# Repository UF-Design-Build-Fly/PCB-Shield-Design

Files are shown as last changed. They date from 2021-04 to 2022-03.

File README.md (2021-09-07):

# PCB-Shield-Design Description
Custom "Shield" Design to be mounted on MicroMod ATP Carrier board seen in Avionics Repo. Here are its [dimensions](https://cdn.sparkfun.com/assets/4/8/6/f/7/MicroMod_ATP_Carrier_Board_Dimensions.png).

## Features v2
- Sensors on board: IMU, pressure, temperature, voltage, current, airspeed. 
- 3 pin connectors for servos. 
- PWM signals from receiver are wired to the board and routed to the servos.
- Female headers will connect the shield to the carrier board (stacking boards).
- PWM signals will be wired to I/O pins to be read and logged.
- Micro SD will be used for data logging.
- Power for avionics and servos will be separate.
- Step down buck converter will be used to regulate a 5V supply voltage on the board (5V will also be fed to VIN for carrier board to be stepped down to 3.3V).
- Mounting holes on corners of the board (100 mil diameter).
- 2 LED light indicators to communicate state of device.

TOP 3D             |  TOP PCB
:-------------------------:|:-------------------------:
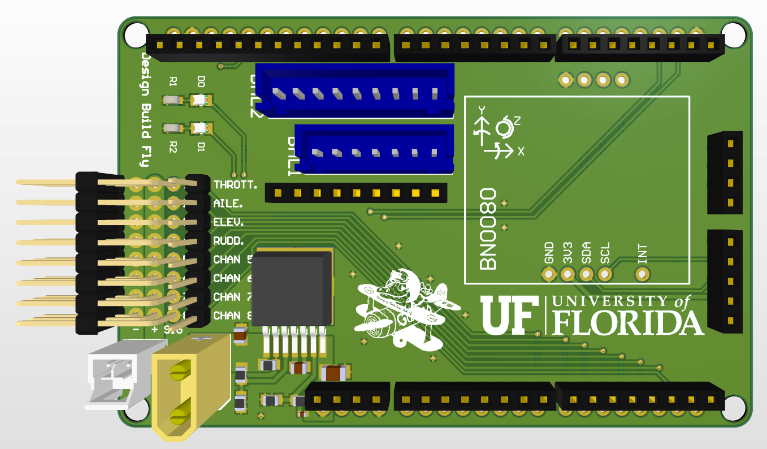
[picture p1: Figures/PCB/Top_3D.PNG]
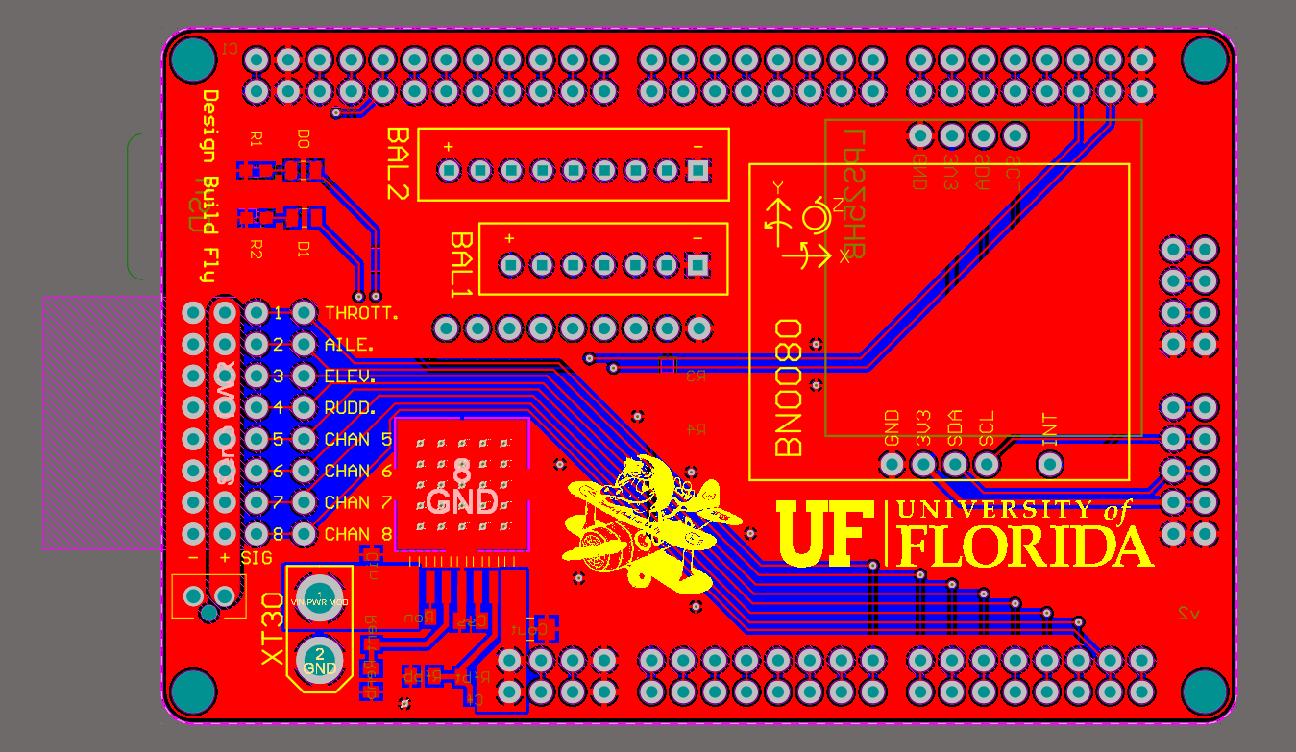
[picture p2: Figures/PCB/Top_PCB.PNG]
  |  

BOTTOM 3D             |  BOTTOM PCB
:-------------------------:|:-------------------------:
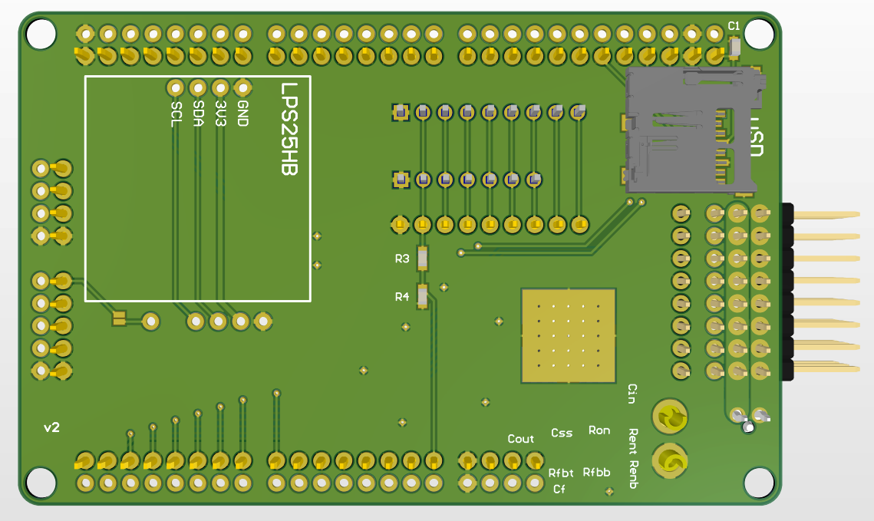
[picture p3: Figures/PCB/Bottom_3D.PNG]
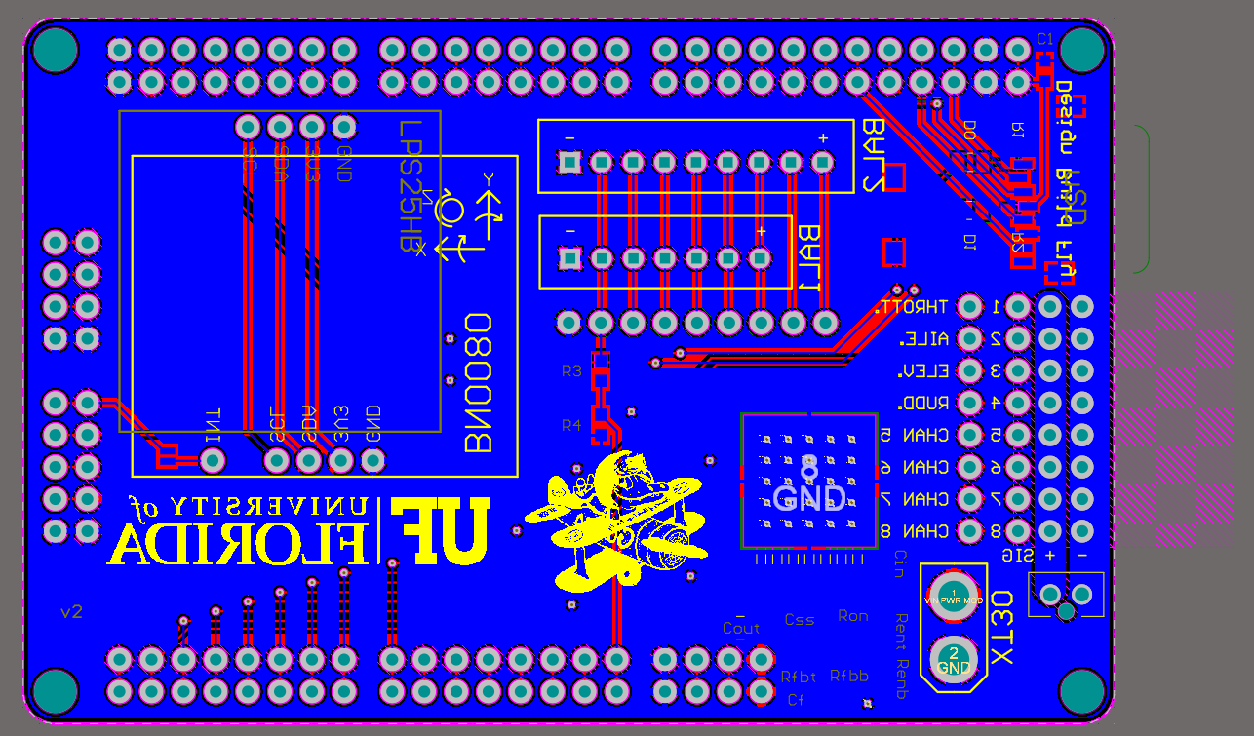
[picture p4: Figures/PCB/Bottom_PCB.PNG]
  |  

## v3 Revisions
- Remove unnecessary parts on PCB: JST connectors for battery balance leads, alarm connector, voltage divider for monitoring 1st cell on battery, any useless female connectors that can free up space (e.g. we are not using I2S connectors or any UART but we are using I2C, etc.).
- Remove solder mask on servo PWR and GND. Change trace width to somewhere between 80 and 90 mil. Decide whether custom copper bus bar or a layer of solder will be used to increase the amount of current the traces can carry. Solder can be around 10 times less conductive resulting in greater power loss, but it is the simpler solution (silver solder is only around 5 to 2.5 times less conductive). Copper bus bar is the more complex solution and involves machining or plasma cutting bus bars from sheets of copper and then connecting them to the board with a thin layer of solder for an adequate connection. This solution provides better power delivery and will result in less heat being generated. Or we can just add a wire on top for the pins ```\ ___ :/ ___ /````
- Add connectors for airspeed sensor and voltage/current sensor
- Look at signal connections between receiver and board. Determine what type of molex connector should be used for a secure connection. 
- Decide on dedicated pin usage for PCB. 
- Should the width of the board be increased?
- Correct screw size for 0.1 inch.
- Servo PWR connector should be XT30
- Determine whether or not XT30 connectors should be horizontal and not vertical.
- Change Rfbb resistor (must be between 1k and 10k) on buck converter to a potentiometer. Probably buy a 2k potentiometer with a screw terminal. This allows us to tune the output voltage to 5V.
- Add power LED at Vout of LMZ12002
- Add piezo for sounds?

## Additional Ideas?
- Make another small board to send signals from angle of attack sensor

## Dedicated Pin Usage (e.g. General I/O, Analog and digital pins, SPI pins, I2C pins)
TBD

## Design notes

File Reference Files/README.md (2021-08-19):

## Viewing PCBs
If you do not have Altium Designer go to Altium Viewer to view the files under "Import Files": https://www.altium.com/viewer/#features

### Things to remember
- 1 mil = 1 thousandth of an inch
- Standard pitch is 0.1 inches or 2.54 mm
- SparkFun's hole shape is round, top: 74mil, hole size: 40mil

When needed, calculate trace width using this [webiste](https://www.4pcb.com/trace-width-calculator.html)'

## Connector Info
- Lipo Balance Leads: [JST-XH](https://www.digikey.com/catalog/en/partgroup/xh-series/2841)
  - [6s](https://www.digikey.com/en/products/detail/jst-sales-america-inc/B7B-XH-A-LF-SN/1651050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)
  - [8s](https://www.digikey.com/en/products/detail/jst-sales-america-inc/B9B-XH-A(LF)(SN)/1651042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)
  - [CAD files](https://www.jst-mfg.com/product/detail_e.php?series=277) for 6s and 8s connector
- Servo PWR connector (Header): [1053091202](https://www.digikey.com/en/products/detail/molex/1053091202/6131607)
- Servo PWR connector (Recepticle): [1053071202](https://www.molex.com/molex/products/part-detail/crimp_housings/1053071202)
- Servo PWR connector (Crimp Terminal): [1053002200](https://www.molex.com/molex/products/part-detail/crimp_terminals/1053002200)
- Other Power Connectors: [MOLEX](https://www.molex.com/molex/products/group/wire_to_board_connectors)

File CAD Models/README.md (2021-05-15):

## Links to external CAD files
Tripe row male header pins (pitch 2.54mm): https://grabcad.com/library/triple-row-male-pin-headers-1

XH Connector : https://www.jst-mfg.com/product/detail_e.php?series=277

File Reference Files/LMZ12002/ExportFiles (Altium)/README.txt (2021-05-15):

## WEBENCH Design 4
Created at Sat May 15 13:25:19 PDT 2021
**********************************************************
***************** Schematic Instructions  ****************
**********************************************************

To import your new Schematic into Altium:

1. Unzip the downloaded folder files to a local directory and 
   Start the Altium program.
2. From the menu select "File"->"Open".
3. Select the file named in the path above ending with ".schdoc"
   and "Open" the file.
4. Your Schematic should be viewable within Altium now.

For additional information, please visit this site:
http://www.accelerated-designs.com/help/Altium_BrdSch_import.html

**********************************************************
*******************  PCB Instructions  *******************
**********************************************************

To import your new BOARD into Altium:

1. Unzip the downloaded folder files to a local directory
	and Start the Altium program.
2. From the menu select "File"->"Open".
3. Select the file named in the path above ending with ".pcbdoc"
   and "Open" the file.
4. Planes will need to be repoured to update the Copper Pour Polygons
	a. Once your board is loaded, select the Tools menu from the
	   top Menu Bar
	b. Scroll to the Polygon Pours item on the Tools Menu.
	c. The Polygon Pours item should expand to show more options
	d. Select Repour All Polygons, this will repour all of the
	   polygons.
5. Your board should be viewable within Altium now.

For additional information, please visit this site:
http://www.accelerated-designs.com/help/Altium_BrdSch_import.html

**********************************************************
*******************  LIB Instructions  *******************
**********************************************************

To import your new LIBRARY PARTS into Altium follow these steps:

1. After running the Ultra Librarian export for the first time,
   you will need to copy the following files into an area where
   they can be accessed for all future translations.  They are script
   files that Altium will need to be able to find.
	a. UL_Form.dfm
	b. UL_Form.pas
	c. UL_Import.pas
	d. UL_Import.prjScr
2. The above script file will need to be run from within Altium.
   This can be done by going to File, Open and selecting the
   UL_Import.PrjScr file stored above.
3. Select the "DXP" dropdown menu in the top-left corner runfrom
   the drop down menu and select "Run Script". Select "UL_Form.pas"
   and click "OK"
4. When the script is run, it will ask you for the file name of the
   Ultra Librarian file to run. Click "File...", select the latest file
   produced with a date code (for instance 2010-02-17_23-12-34.txt), and
   click "Start Import".
5. The script will open a new Integraged Library project and import
   the Ultra Librarian data into it.  When complete a message box
   will pop up saying that import is done.

For additional information, please visit this site:
http://www.accelerated-designs.com/help/Altium_import.html

For a video tutorial, please visit:
http://youtu.be/pih50yx9HYU

**********************************************************
****************  SIMULATION Instructions  ***************
**********************************************************
This XML can be imported in Altium Designer 14 and higher using
WEBENCH Altium Connector Extension and simulated using WEBENCH
Simulation Engine.

The WEBENCH Altium Connector provides an interface to the
Texas Instruments WEBENCH Designer Tools as well as to open
WEBENCH exported Designs directly from inside Altium Designer.
It also includes the advanced WEBENCH Simulation Engine which
can be used for offline circuit simulations.

You will need to activate WEBENCH Altium Connector to be able
to use the WEBENCH Simulation Engine.

Installation guide:
http://www.ti.com/lit/SNVU481
You can download the WEBENCH extension from Altium Designer Extensions.

Connector Details:
http://www.ti.com/lsds/ti/analog/webench/altiumconnector.page

More about WEBENCH simulation export to Altium:
http://www.ti.com/lsds/ti/analog/webench/simexportaltium.page

User Manual:
http://www.ti.com/lit/szzu007

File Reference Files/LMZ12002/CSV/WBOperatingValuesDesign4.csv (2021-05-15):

Name | Value | Category | Description
Vout | 5 V | System Information | Operational Output Voltage
IC Tolerance | 20 mV | IC | IC Feedback Tolerance
Cin IRMS | 489.25 mA | Capacitor | Input capacitor RMS ripple current
Cin Pd | 957.44 µW | Capacitor | Input capacitor power dissipation
Cout IRMS | 119.17 mA | Capacitor | Output capacitor RMS ripple current
Cout Pd | 40.3 µW | Capacitor | Output capacitor power dissipation
Duty Cycle | 60.31% | System Information | Duty cycle
Efficiency | 91.8% | System Information | Steady state efficiency
Frequency | 488.71 kHz | System Information | Switching frequency
IC Tj | 43.6 °C | IC | IC junction temperature
ICThetaJA | 19.3 °C/W | IC | IC junction-to-ambient thermal resistance
IC Pd | 445.62 mW | IC | IC power dissipation
Pout | 5 W | System Information | Total output power
Iin Avg | 633.33 mA | IC | Average input current
IC Ipk | 1.21 A | IC | Peak switch current in IC
Mode | CCM | System Information | Conduction Mode
Vout p-p | 1.17 mV | System Information | Peak-to-peak output ripple voltage
M Vds Act | 130 mV | Mosfet | Voltage drop across the MosFET
M Irms | 852.42 mA | Mosfet | MOSFET RMS current
Total Pd | 446.62 mW | Power | Total Power Dissipation
FootPrint | 260 mm² | System Information | Total Foot Print Area of BOM components
Vin | 8.6 V | System Information | Vin operating point
Iout | 1 A | System Information | Iout operating point
Cin Pd | 957.44 µW | Power | Input capacitor power dissipation
Cout Pd | 40.3 µW | Power | Output capacitor power dissipation
IC Pd | 445.62 mW | Power | IC power dissipation
Vout Actual | 5 V | System Information | Vout Actual calculated based on selected voltage divider resistors
Vout Tolerance | 4.24% | System Information | Vout Tolerance based on IC Tolerance (no load) and voltage divider resistors if applicable
Total BOM | $4.66 | System Information | Total BOM Cost
BOM Count | 10 | System Information | Total Design BOM count

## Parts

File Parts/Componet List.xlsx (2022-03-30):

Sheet: PCB_Shield_v2
Componet Name | Manufacture No. | Description | Quantity | Unit Price | Link (if applicable) | Find Resistors: https://www.digikey.com/en/products/filter/chip-resistor-surface-mount/52
ERJ-3EKF1051V | ERJ-3EKF1051V | RES SMD 1.05K OHM 1% 1/10W 0603 | 1 | $0.10 | https://www.digikey.com/en/products/detail/panasonic-electronic-components/ERJ-3EKF1051V/196035 | Find Capacitors: https://www.digikey.com/en/products/filter/ceramic-capacitors/60
ERJ-3EKF3000V | ERJ-3EKF3000V | RES SMD 300 OHM 1% 1/10W 0603 | 1 | $0.10 | https://www.digikey.com/en/products/detail/panasonic-electronic-components/ERJ-3EKF3000V/1746363
RMCF0603JT10K0 | RMCF0603JT10K0 | RES 10K OHM 5% 1/10W 0603 | 2 | $0.10 | https://www.digikey.com/en/products/detail/stackpole-electronics-inc/RMCF0603JT10K0/1758104
LM338T/NOPB | LM338T/NOPB | IC REG LINEAR POS ADJ 5A TO220-3 | 1 | $2.23 | https://www.digikey.com/en/products/detail/texas-instruments/LM338T-NOPB/212669
CL10B104KB8NNNC | CL10B104KB8NNNC | CAP CER 0.1UF 50V X7R 0603 | 2 | $0.10 | https://www.digikey.com/en/products/detail/samsung-electro-mechanics/CL10B104KB8NNNC/3886658
CGB3B1X7R1A105K055AC | CGB3B1X7R1A105K055AC | CAP CER 1UF 10V X7R 0603 | 1 | $0.20 | https://www.digikey.com/en/products/detail/tdk-corporation/CGB3B1X7R1A105K055AC/3950464
MicroSD Socket | PRODUCT ID: 1660 | Add tons of storage to your next project with this micro SD card socket. We use this part in all our designs and it works great with any microSD ('transflash') of any storage size. It's a surface-mount part and the pins are underneath so it needs a fine tip and paste or thin solder to get in there and solder, not for beginners! It is a push-push type: push the card in to insert, push again to spring it out. | 1 | $1.95 | https://www.adafruit.com/product/1660
XT30 Connector (Male) | N/A | N/A | 1 | $0.39 | https://www.racedayquads.com/products/xt30-connector-male-or-female?_pos=11&_sid=ba0a2201c&_ss=r
S7B-XH-A(LF)(SN) | S7B-XH-A(LF)(SN) | CONN HEADER R/A 7POS 2.5MM | 1 | $0.61 | https://www.digikey.com.au/product-detail/en/jst-sales-america-inc/S7B-XH-A-LF-SN/455-2240-ND/1651038
B2B-XH-A(LF)(SN) | B2B-XH-A(LF)(SN) | CONN HEADER VERT 2POS 2.5MM | 1 | $0.15 | https://www.digikey.com/en/products/detail/jst-sales-america-inc/B2B-XH-A-LF-SN/1651045
LEDs w/ current limiting resistor | https://www.digikey.com/en/products/filter/led-indication-discrete/105
150080YS75000 | 150080YS75000 | LED YELLOW CLEAR 0805 SMD | 1 | $0.18 | https://www.digikey.com/en/products/detail/w%C3%BCrth-elektronik/150080YS75000/4489927
150080RS75000 | 150080RS75000 | LED RED CLEAR 0805 SMD | 1 | $0.18 | https://www.digikey.com/en/products/detail/w%C3%BCrth-elektronik/150080RS75000/4489918
150080VS75000 | 150080VS75000 | LED GREEN CLEAR 0805 SMD | 1 | $0.18 | https://www.digikey.com/en/products/detail/w%C3%BCrth-elektronik/150080VS75000/4489924
ERJ-3EKF66R5V | ERJ-3EKF66R5V | RES SMD 66.5 OHM 1% 1/10W 0603 | 3 | $0.10 | https://www.digikey.com/en/products/detail/panasonic-electronic-components/ERJ-3EKF66R5V/196443

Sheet: PCB_Shield_v3
Part # | Link | Spec | Description | Qty | Package | Need to Order (Y/N) | In Altium | Datasheet
TSR 1-2450 | https://www.digikey.com/en/products/detail/traco-power/TSR-1-2450/9383780 | 5V 1A Output | Buck Converter | 1 | N/A | Y | N | https://www.tracopower.com/sites/default/files/products/datasheets/tsr1_datasheet.pdf
XT30 right angle connector | https://www.amazon.com/Amass-XT30PW-Upgrade-Connectors-Battery/dp/B099F2PXYN | XT30 | Avionics Battery Connector | 1 | N/A | N | N | https://www.amazon.com/Amass-XT30PW-Upgrade-Connectors-Battery/dp/B099F2PXYN

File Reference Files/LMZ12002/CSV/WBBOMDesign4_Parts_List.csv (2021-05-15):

Part | Manufacturer | Part Number | Quantity | Price ($) | Footprint (mm²) | Description
Cf | MuRata | GRM1555C1H102JA01J | 1 | 0.01 | 3 | Cap: 1 nF Total Derated Cap: 1 nF VDC: 50 V ESR: 0 Ω Package: 0402
Cin | MuRata | GRM21BR61E106MA73L | 1 | 0.05 | 6.75 | Cap: 10 µF Total Derated Cap: 2.7 µF VDC: 25 V ESR: 4 mΩ Package: 0805
Cout | TDK | C3216X5R1A107M160AC | 1 | 0.5 | 10.92 | Cap: 100 µF Total Derated Cap: 50 µF VDC: 10 V ESR: 2.84 mΩ Package: 1206_190
Css | MuRata | GRM21BR71H473KA01L | 1 | 0.02 | 6.75 | Cap: 47 nF Total Derated Cap: 47 nF VDC: 50 V ESR: 1 mΩ Package: 0805
Renb | Panasonic | ERJ-6ENF6981V | 1 | 0.01 | 6.75 | Resistance: 6.98 kΩ Tolerance: 1.0% Power: 125 mW
Rent | Vishay-Dale | CRCW080534K0FKEA | 1 | 0.01 | 6.75 | Resistance: 34 kΩ Tolerance: 1.0% Power: 125 mW
Rfbb | Panasonic | ERJ-6ENF1071V | 1 | 0.01 | 6.75 | Resistance: 1.07 kΩ Tolerance: 1.0% Power: 125 mW
Rfbt | Panasonic | ERJ-6ENF5621V | 1 | 0.01 | 6.75 | Resistance: 5.62 kΩ Tolerance: 1.0% Power: 125 mW
Ron | Vishay-Dale | CRCW080578K7FKEA | 1 | 0.01 | 6.75 | Resistance: 78.7 kΩ Tolerance: 1.0% Power: 125 mW
U1 | Texas Instruments | LMZ12002TZ-ADJ/NOPB | 1 | 4.025 | 198.82

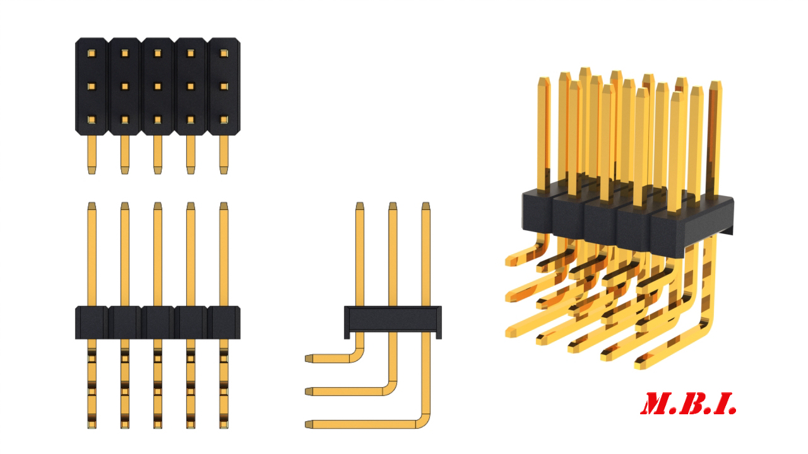
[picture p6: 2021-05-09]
CAD Models/Components/Triple Row Male Header Pins/Renderings/Triple Row Male Pin Headers IMG_03.JPG

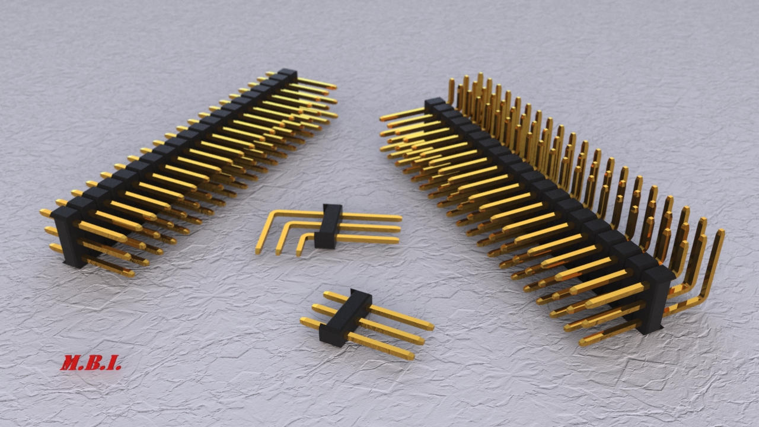
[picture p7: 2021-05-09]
CAD Models/Components/Triple Row Male Header Pins/Renderings/Triple Row Male Pin Headers IMG_01.JPG

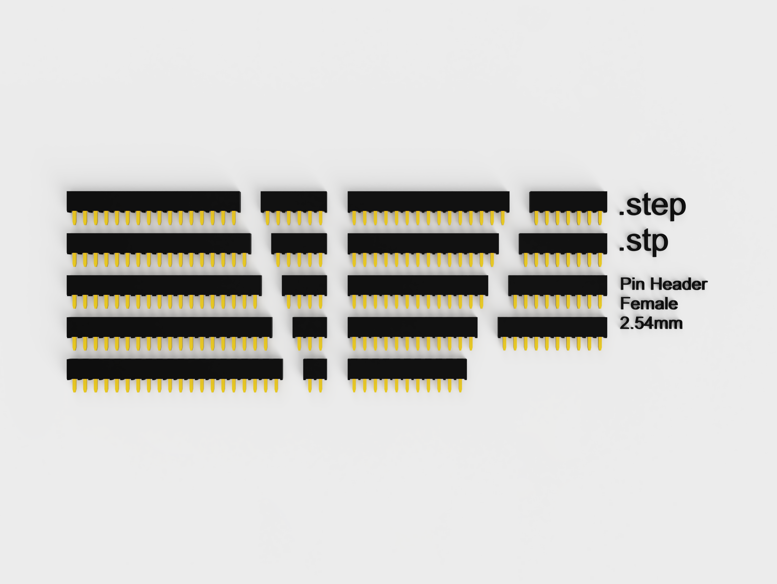
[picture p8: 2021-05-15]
CAD Models/Components/Single Row Female Header Pins/Pin_Header-Female-2.54mm_V3.png

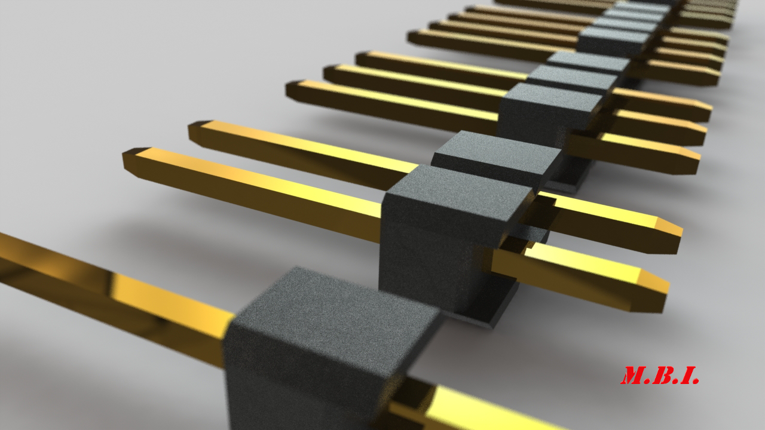
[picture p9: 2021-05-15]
CAD Models/Components/Signle Row Male Header Pins/Renderings/Single Row Male Pin Headers IMG_01.JPG

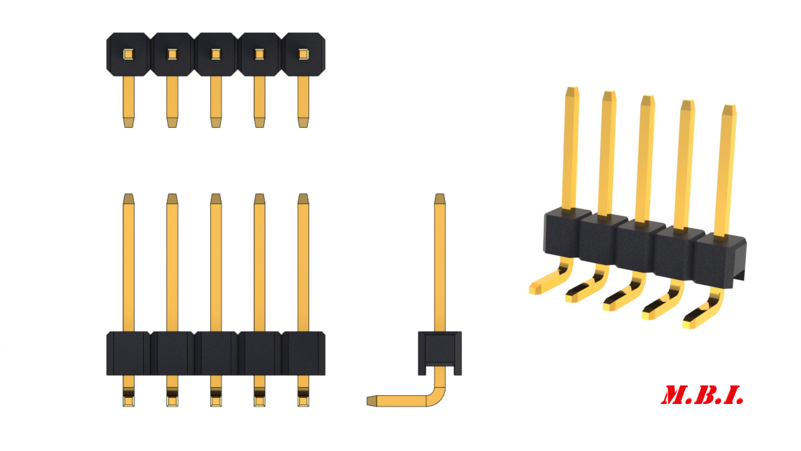
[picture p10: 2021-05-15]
CAD Models/Components/Signle Row Male Header Pins/Renderings/Single Row Male Pin Headers IMG_05.JPG

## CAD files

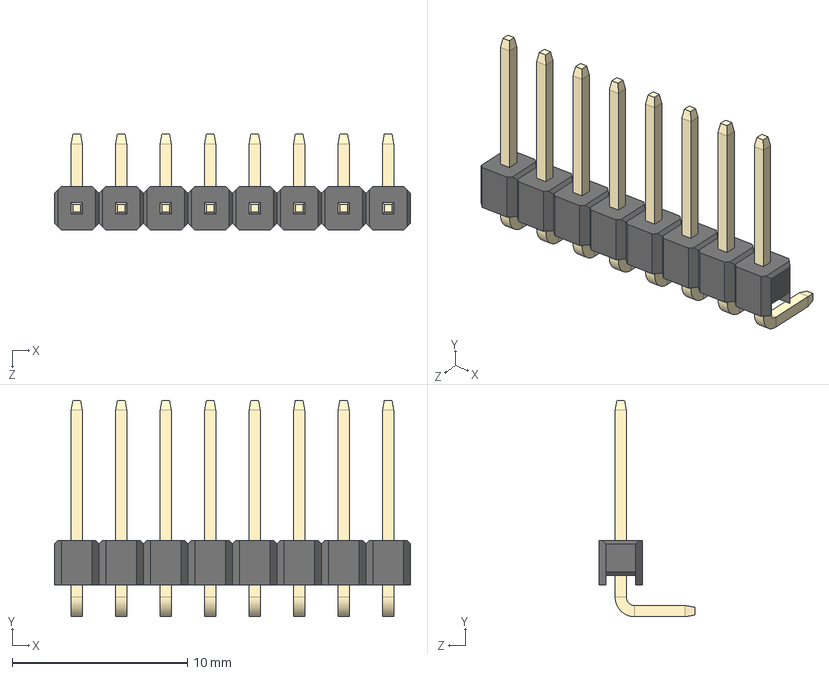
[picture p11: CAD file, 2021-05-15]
CAD Models/Components/Signle Row Male Header Pins/1x8 Male Pin Header Angle.STEP
20.3 x 12.4 x 5.50 mm

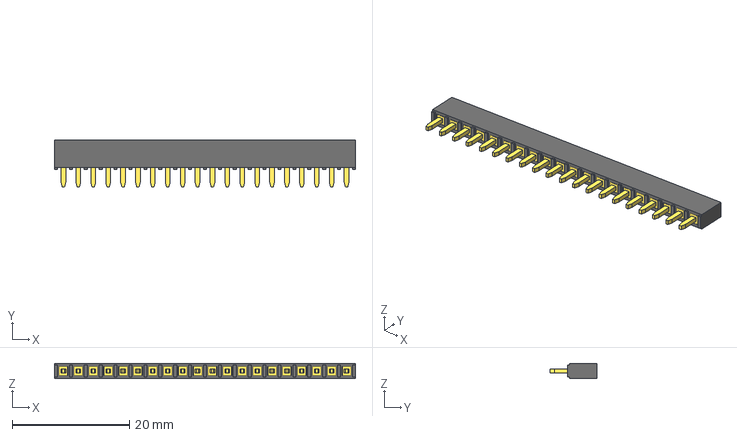
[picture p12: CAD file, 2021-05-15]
CAD Models/Components/Single Row Female Header Pins/20-Pin Header - Female - 2.54mm.step
51.3 x 8.00 x 2.50 mm

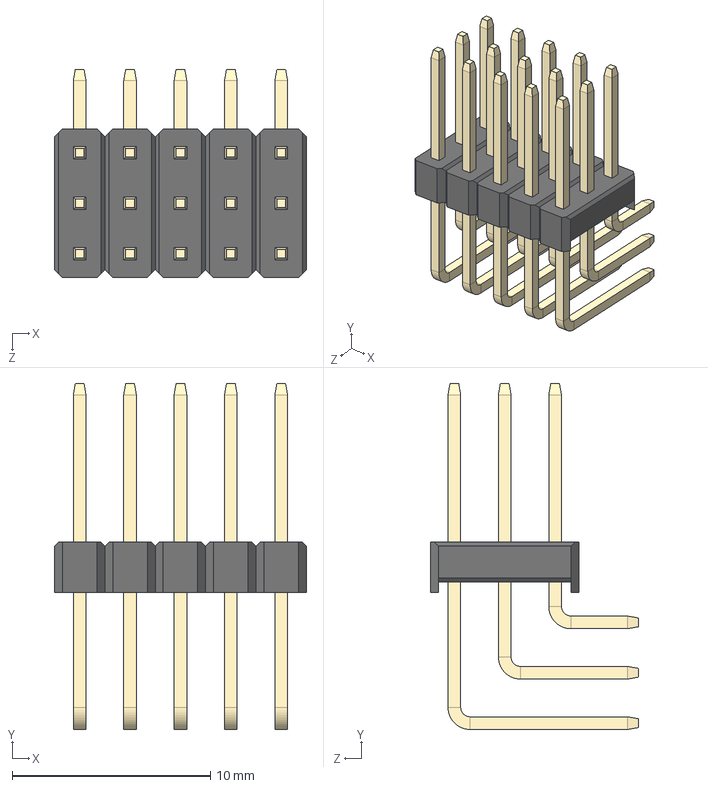
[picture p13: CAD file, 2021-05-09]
CAD Models/Components/Triple Row Male Header Pins/3x5 Male Pin Header Angle.STEP
12.7 x 17.4 x 10.5 mm

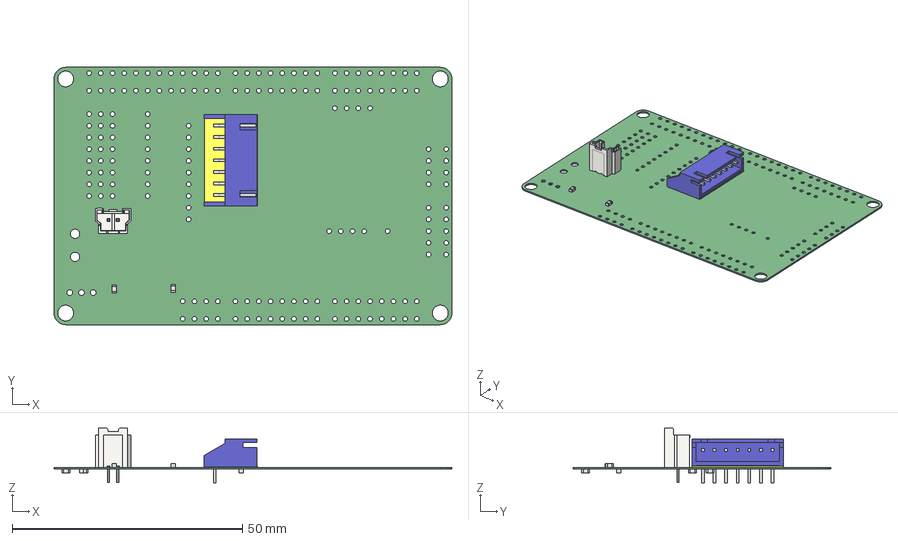
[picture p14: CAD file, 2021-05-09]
CAD Models/PCB_Shield_v1.step
86.4 x 55.9 x 11.9 mm
Extruded x 22
S7B-XH-A

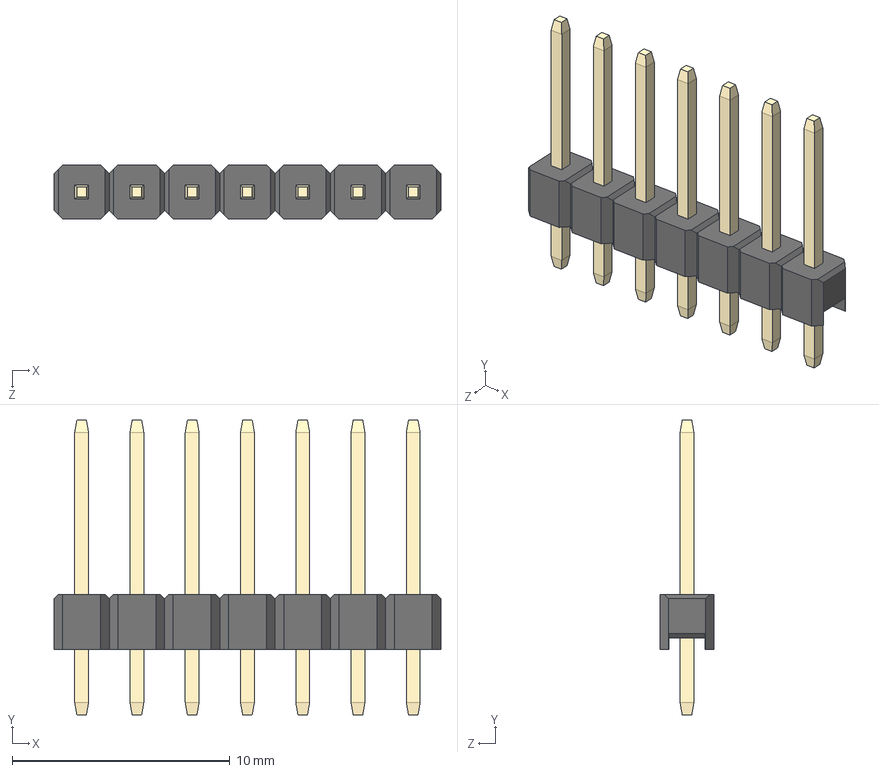
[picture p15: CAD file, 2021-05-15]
CAD Models/Components/Signle Row Male Header Pins/1x7 Male Pin Header.STEP
17.8 x 13.5 x 2.50 mm

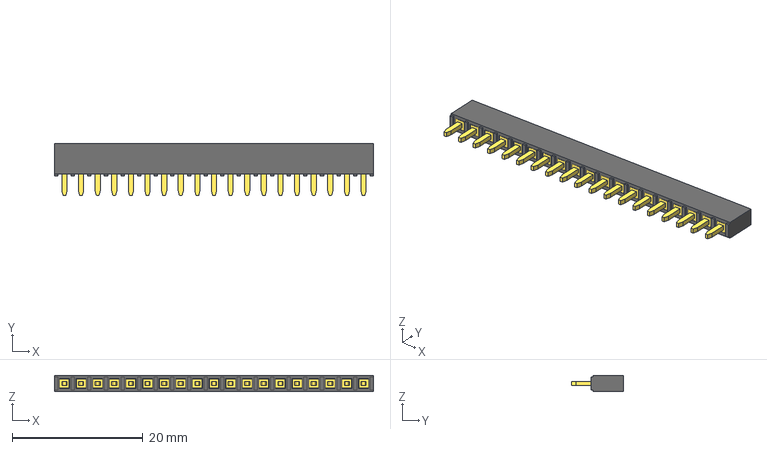
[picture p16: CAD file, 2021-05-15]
CAD Models/Components/Single Row Female Header Pins/19-Pin Header - Female - 2.54mm.step
48.8 x 8.00 x 2.50 mm

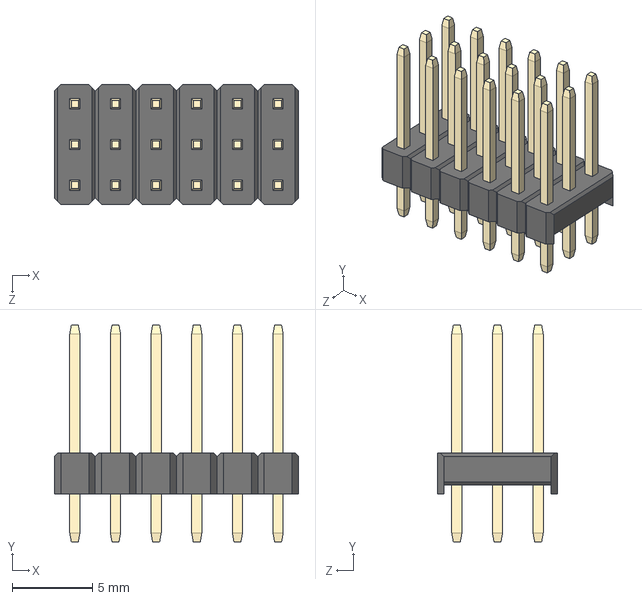
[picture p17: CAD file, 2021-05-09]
CAD Models/Components/Triple Row Male Header Pins/3x6 Male Pin Header.STEP
15.2 x 13.5 x 7.50 mm

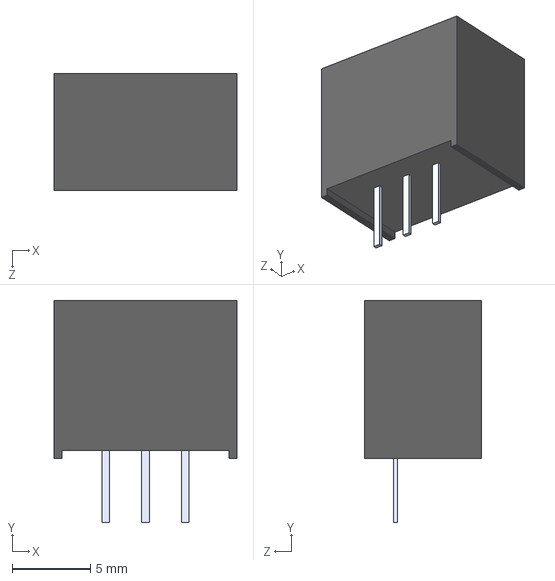
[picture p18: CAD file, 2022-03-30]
CAD Models/Components/TSR 1-2450.STEP
11.7 x 14.2 x 7.50 mm

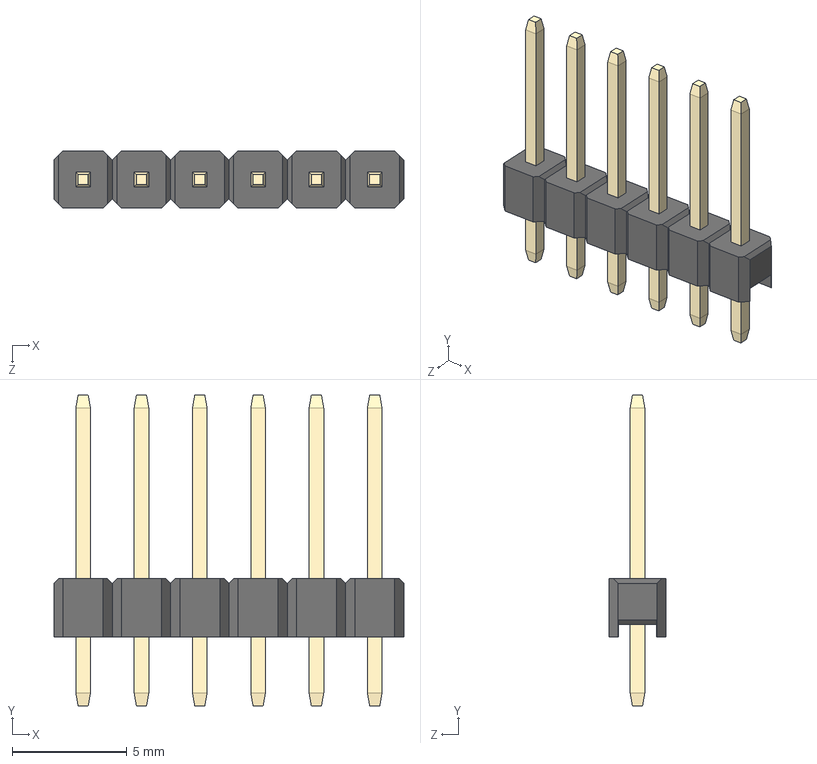
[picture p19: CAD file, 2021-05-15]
CAD Models/Components/Signle Row Male Header Pins/1x6 Male Pin Header.STEP
15.2 x 13.5 x 2.50 mm

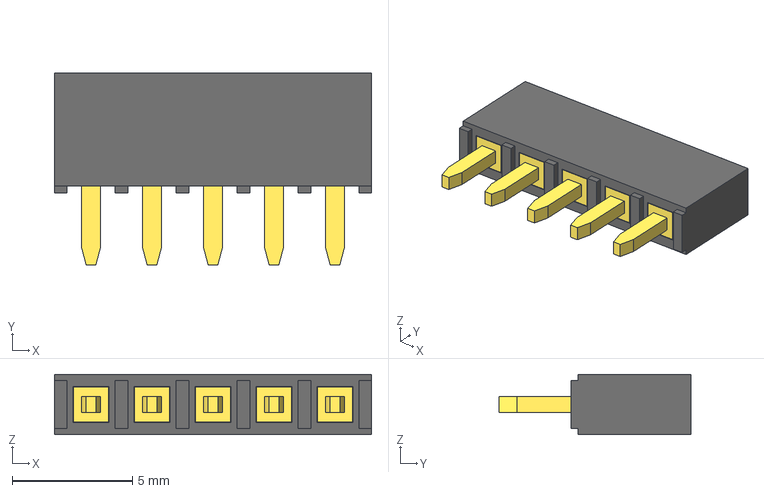
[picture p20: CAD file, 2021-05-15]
CAD Models/Components/Single Row Female Header Pins/5-Pin Header - Female - 2.54mm.step
13.2 x 8.00 x 2.50 mm

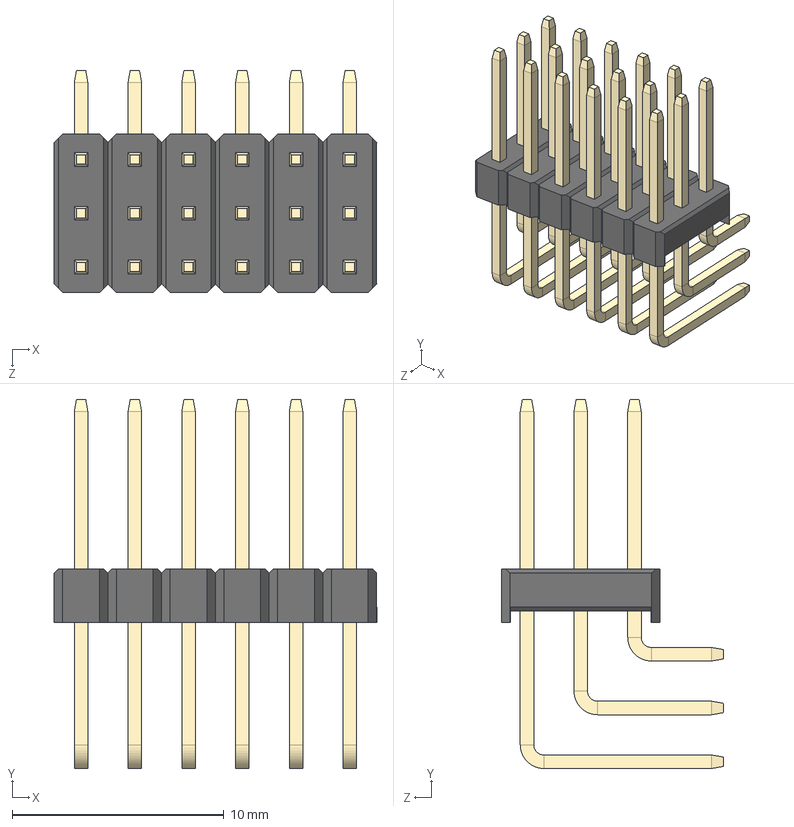
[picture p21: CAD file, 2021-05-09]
CAD Models/Components/Triple Row Male Header Pins/3x6 Male Pin Header Angle.STEP
15.2 x 17.4 x 10.5 mm

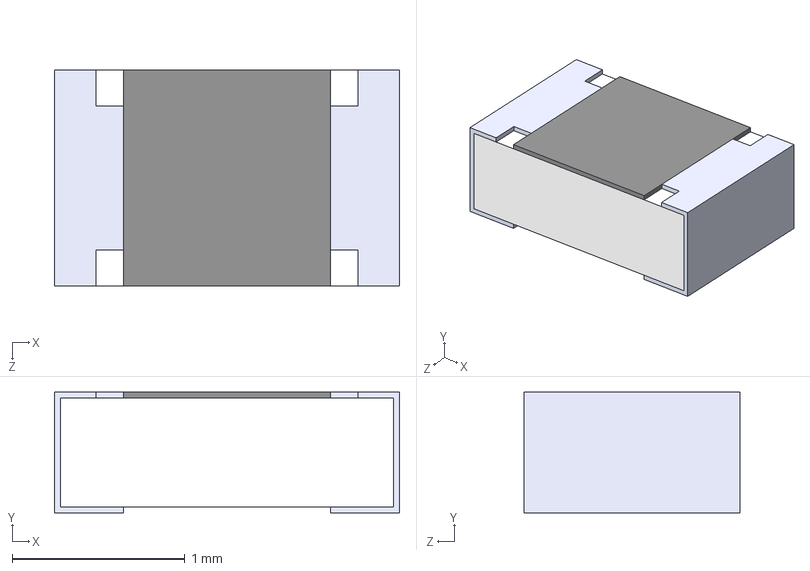
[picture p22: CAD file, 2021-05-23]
CAD Models/Components/ERJ-6ENF1071V.STEP
2.00 x 0.7 x 1.25 mm

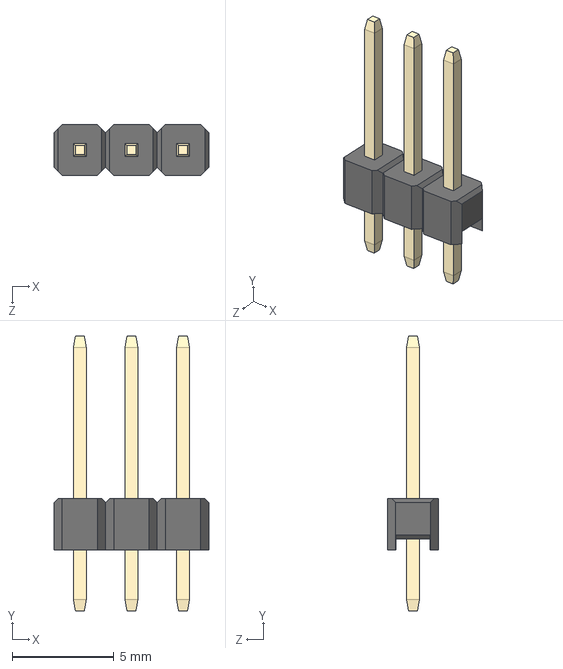
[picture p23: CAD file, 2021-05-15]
CAD Models/Components/Signle Row Male Header Pins/1x3 Male Pin Header.STEP
7.63 x 13.5 x 2.50 mm

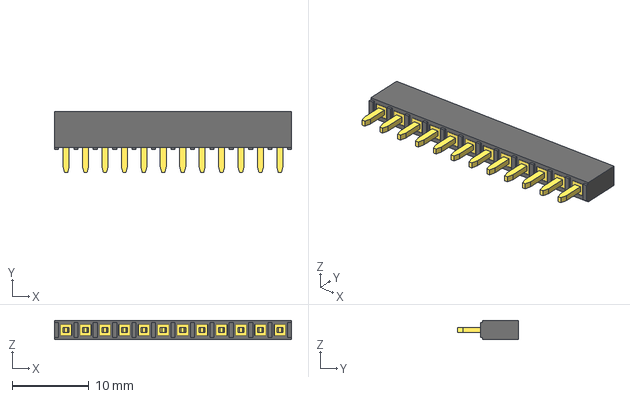
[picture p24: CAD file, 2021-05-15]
CAD Models/Components/Single Row Female Header Pins/12-Pin Header - Female - 2.54mm.step
31.0 x 8.00 x 2.50 mm

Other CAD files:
CAD Models/Components/Triple Row Male Header Pins/3x9 Male Pin Header.STEP
CAD Models/Components/GRM1555C1H102JA01J.STEP
CAD Models/Components/Signle Row Male Header Pins/1x7 Male Pin Header Angle.STEP
CAD Models/Components/Single Row Female Header Pins/8-Pin Header - Female - 2.54mm.step
CAD Models/Components/1053091202.stp
CAD Models/Components/150080AS75000_Download_STP_WL-SMCW-0805_rev1.stp
CAD Models/Components/693071030811_microSD.stp
CAD Models/Components/B7B-XH-A.STEP
CAD Models/Components/B9B-XH-A.STEP
CAD Models/Components/C3216X5R1A107M160AC.STEP
CAD Models/Components/GRM21BR61E106MA73L.STEP
CAD Models/Components/LM338_NOPB.STEP
CAD Models/Components/LMZ12002.stp
CAD Models/Components/Signle Row Male Header Pins/1x1 Male Pin Header Angle.STEP
CAD Models/Components/Signle Row Male Header Pins/1x1 Male Pin Header.STEP
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

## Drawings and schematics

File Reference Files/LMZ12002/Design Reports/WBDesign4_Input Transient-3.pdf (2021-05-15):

## WEBENCH ® Design Report

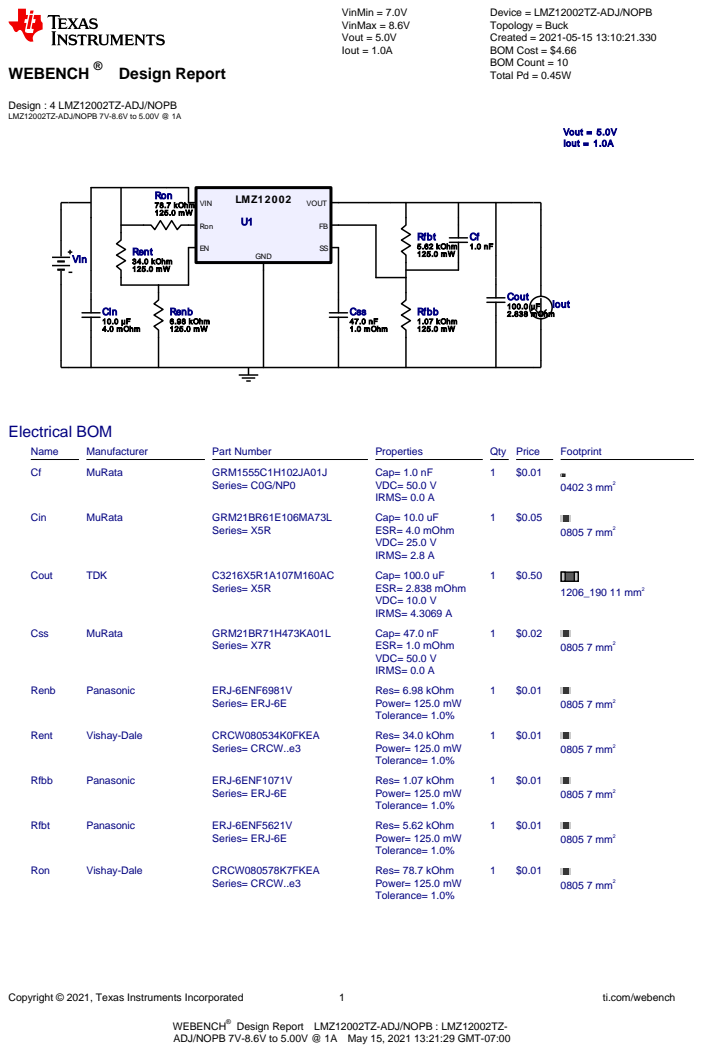
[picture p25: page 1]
Copyright © 2021, Texas Instruments Incorporated; ti.com/webench; VinMin = 7.0V VinMax = 8.6V Vout = 5.0V Iout = 1.0A; Cin 10.0 µF 4.0 mOhm; Cout; 100.0 µF Css; 2.838 mOhm; 47.0 nF 1.0 mOhm; Renb 6.98 kOhm 125.0 mW; Rent 34.0 kOhm 125.0 mW; Rfbb 1.07 kOhm 125.0 mW; Rfbt 5.62 kOhm 125.0 mW; Ron 78.7 kOhm 125.0 mW; LMZ12002 VIN; Ron; VOUT; SS GND; Vout = 5.0V Iout = 1.0A; Vin; Iout; Electrical BOM; Name; Manufacturer; Part Number; Properties; Qty Price; Footprint; MuRata; GRM1555C1H102JA01J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

Device = LMZ12002TZ-ADJ/NOPB
Topology = Buck
Created = 2021-05-15 13:10:21.330
BOM Cost = $4.66
BOM Count = 10
Total Pd = 0.45W

Design : 4 LMZ12002TZ-ADJ/NOPB
LMZ12002TZ-ADJ/NOPB 7V-8.6V to 5.00V @ 1A

WEBENCH®
ADJ/NOPB 7V-8.6V to 5.00V @ 1A May 15, 2021 13:21:29 GMT-07:00

Design Report LMZ12002TZ-ADJ/NOPB : LMZ12002TZ-

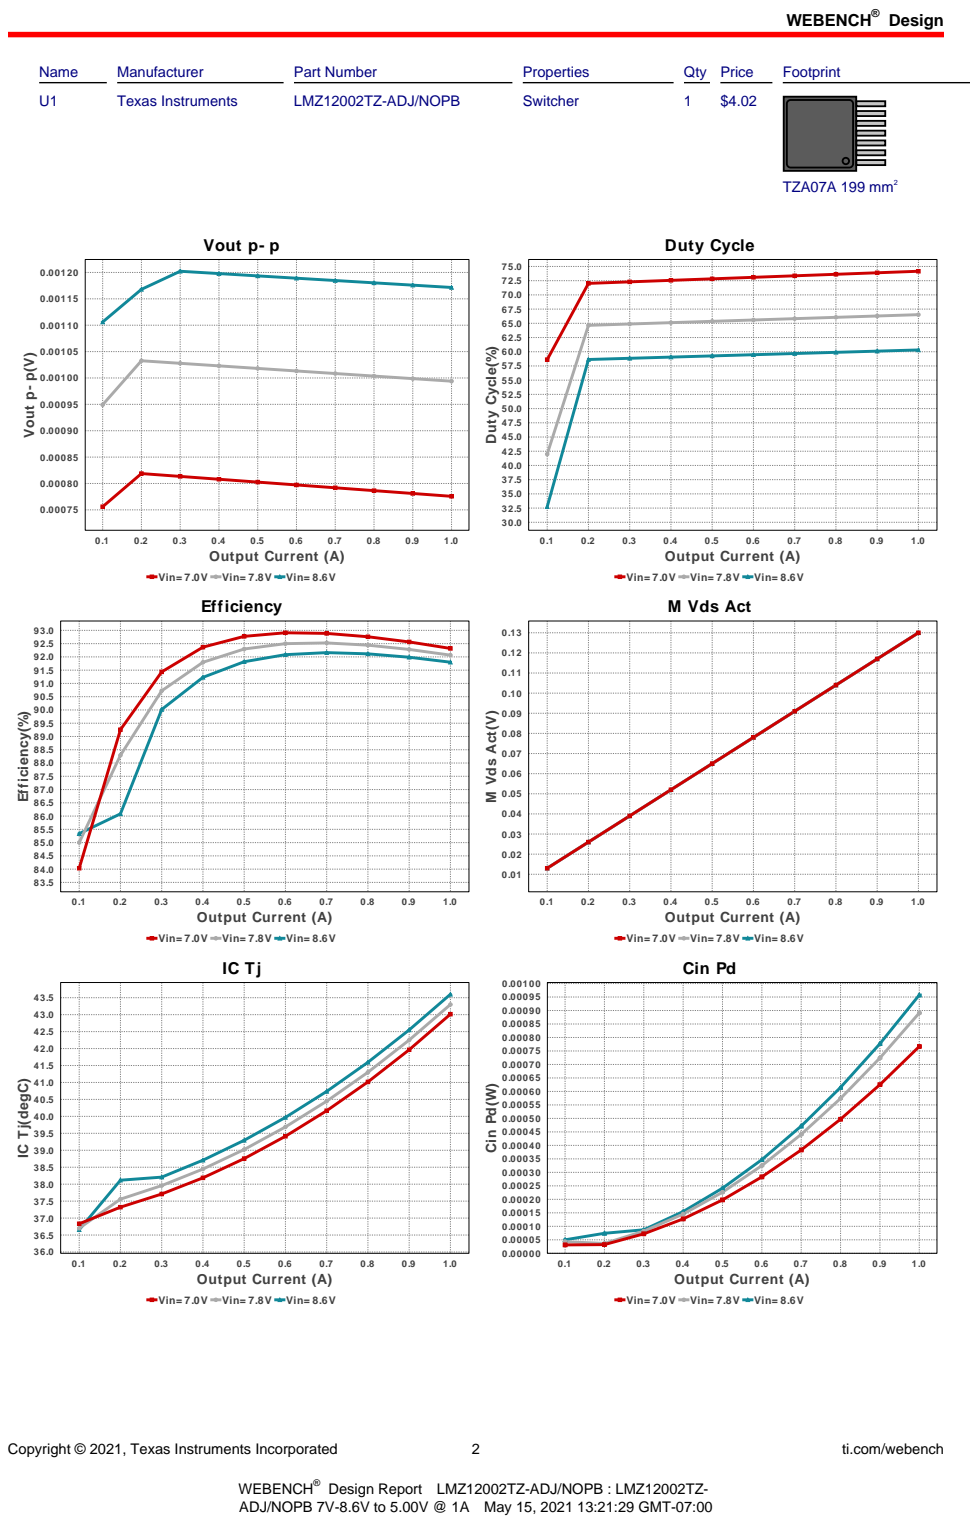
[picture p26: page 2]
Design; Copyright © 2021, Texas Instruments Incorporated; ti.com/webench; Name; Manufacturer; Part Number; Properties; Qty Price; Footprint; Texas Instruments; LMZ12002TZ-ADJ/NOPB; Switcher; TZA07A 199 mm²; Vout p- p; 1.0 Output Current (A); Vout p- p(V); Duty Cycle; Duty Cycle(%); Efficiency(%); M Vds Act(V); Cin Pd(W)

Vin= 7.0V Vin= 7.8V Vin= 8.6V
Efficiency

M Vds Act

Cin Pd

IC Tj(degC)

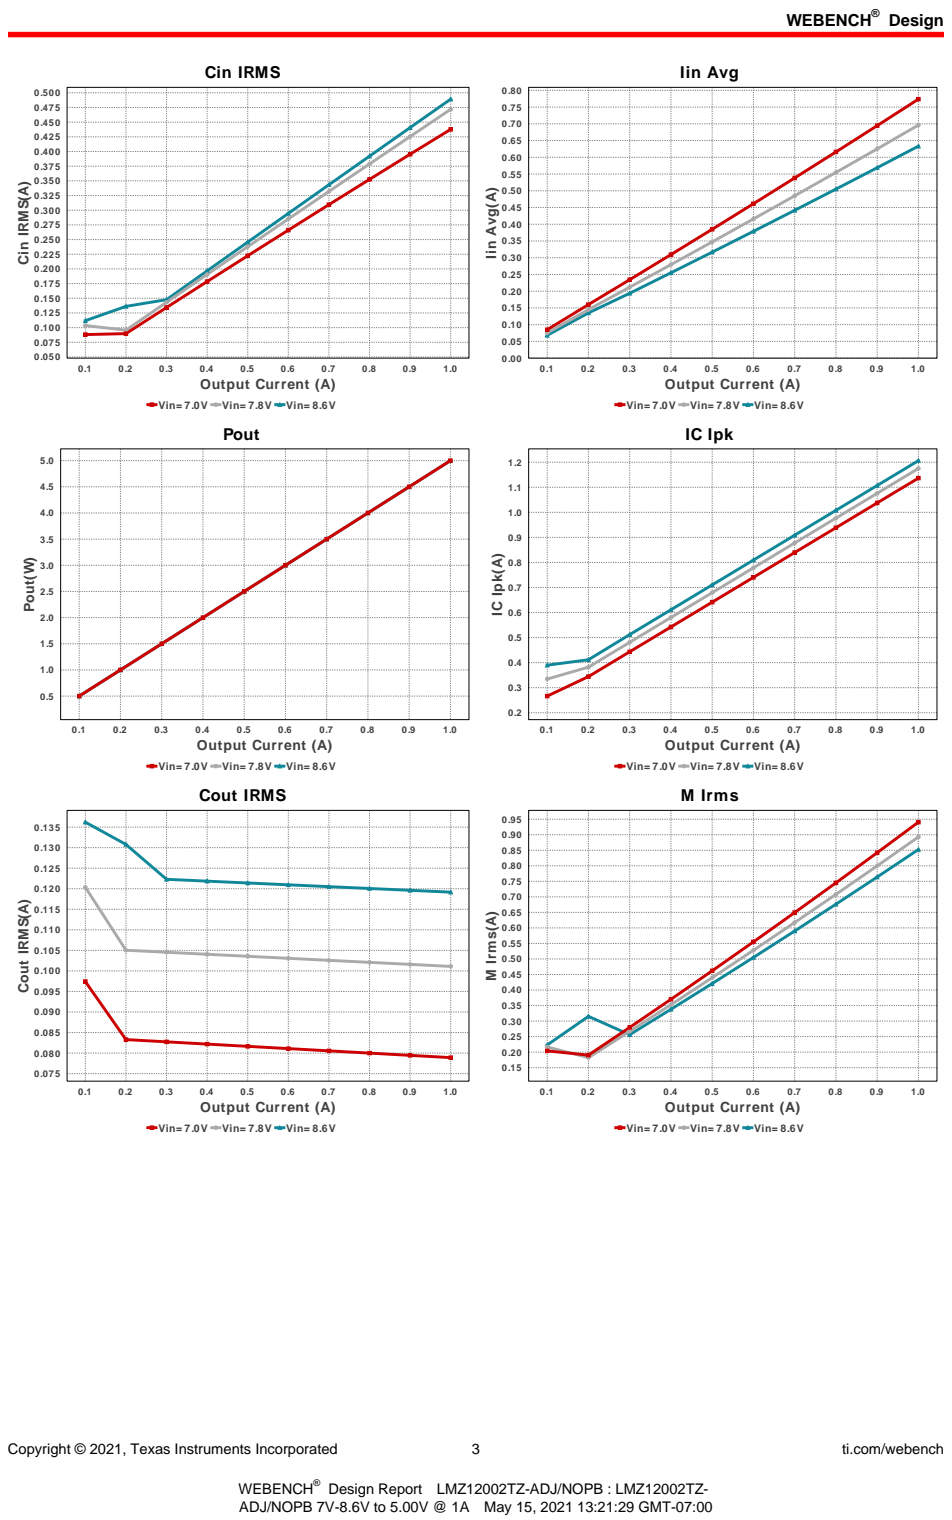
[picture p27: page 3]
Copyright © 2021, Texas Instruments Incorporated; ti.com/webench; Cin IRMS; 1.0 Output Current (A); Cin IRMS(A); Iin Avg; Iin Avg(A); Pout; Pout(W); IC Ipk; IC Ipk(A); Cout IRMS(A); M Irms(A)

Vin= 7.0V Vin= 7.8V Vin= 8.6V

Cout IRMS

M Irms

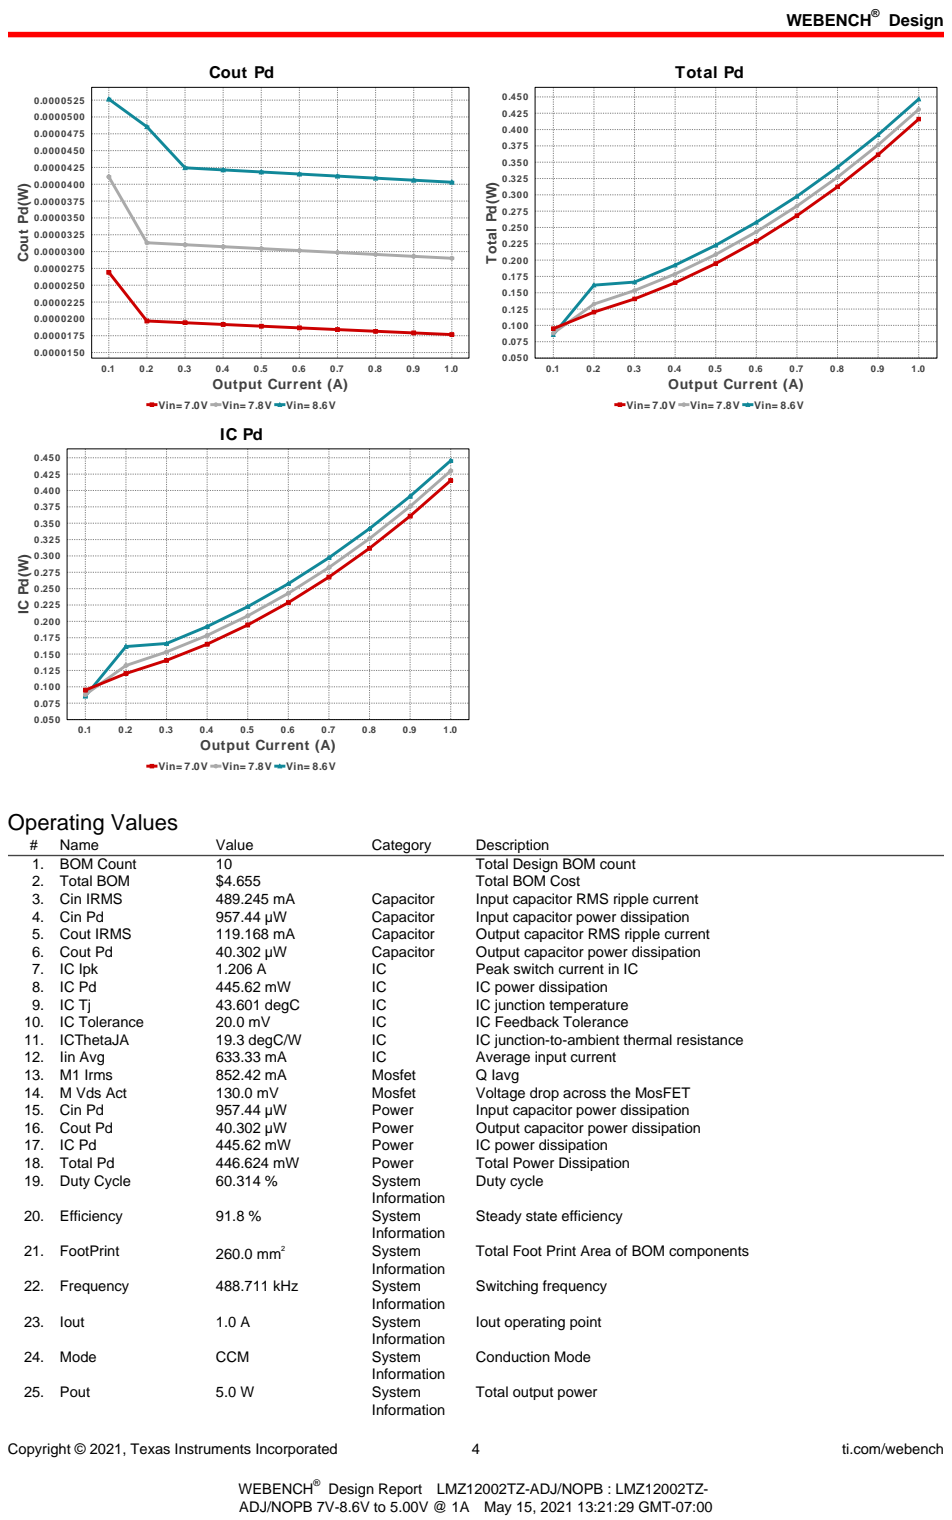
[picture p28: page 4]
Copyright © 2021, Texas Instruments Incorporated; ti.com/webench; Cout Pd; 1.0 Output Current (A); Cout Pd(W); Total Pd; Total Pd(W); Operating Values; Name; Value; Category; Description; 1. BOM Count; Total Design BOM count; 2. Total BOM; Total BOM Cost; 3. Cin IRMS; Capacitor; Input capacitor RMS ripple current; 4. Cin Pd; Input capacitor power dissipation; 5. Cout IRMS; Output capacitor RMS ripple current; 6. Cout Pd; Output capacitor power dissipation; 7. IC Ipk; Peak switch current in IC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

Vin= 7.0V Vin= 7.8V Vin= 8.6V

Steady state efficiency

Total Foot Print Area of BOM components

Iout operating point

Total output power

Copyright © 2021, Texas Instruments Incorporated | 5 | ti.com/webench
# | Name | Value | Category | Description

26. Vin | 8.6 V | System
| | | Information | Vin operating point
27. Vout | 5.0 V | System
| | | Information | Operational Output Voltage
28. Vout Actual | 5.002 V | System
| | | Information | Vout Actual calculated based on selected voltage divider resistors
29. Vout Tolerance | 4.24 % | System
| | | Information | Vout Tolerance based on IC Tolerance (no load) and voltage divider resistors if applicable
30. Vout p-p | 1.172 mV | System
| | | Information | Peak-to-peak output ripple voltage

## Design Inputs

Name | Value | Description
Iout | 1.0 | Maximum Output Current
SoftStart | 5.0 ms | Soft Start Time (ms)
VinMax | 8.6 | Maximum input voltage
VinMin | 7.0 | Minimum input voltage
Vout | 5.0 | Output Voltage
| base_pn | | LMZ12002 | Base Product Number
source | DC | Input Source Type
Ta | 35.0 | Ambient temperature


Copyright © 2021, Texas Instruments Incorporated | 6 | ti.com/webench

## Assembly

## Component Testing

Some published data on components in datasheets such as Capacitor ESR and Inductor DC resistance is based on conservative values that will guarantee that the components always exceed the specification. For design purposes it is usually better to work with typical values. Since this data is not always available it is a good practice to measure the Capacitance and ESR values of Cin and Cout, and the inductance and DC resistance of L1 before assembly of the board. Any large discrepancies in values should be electrically simulated in WEBENCH to check for instabilities and thermally simulated in WebTHERM to make sure critical temperatures are not exceeded.
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

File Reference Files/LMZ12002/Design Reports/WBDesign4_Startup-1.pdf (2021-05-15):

## WEBENCH ® Design Report

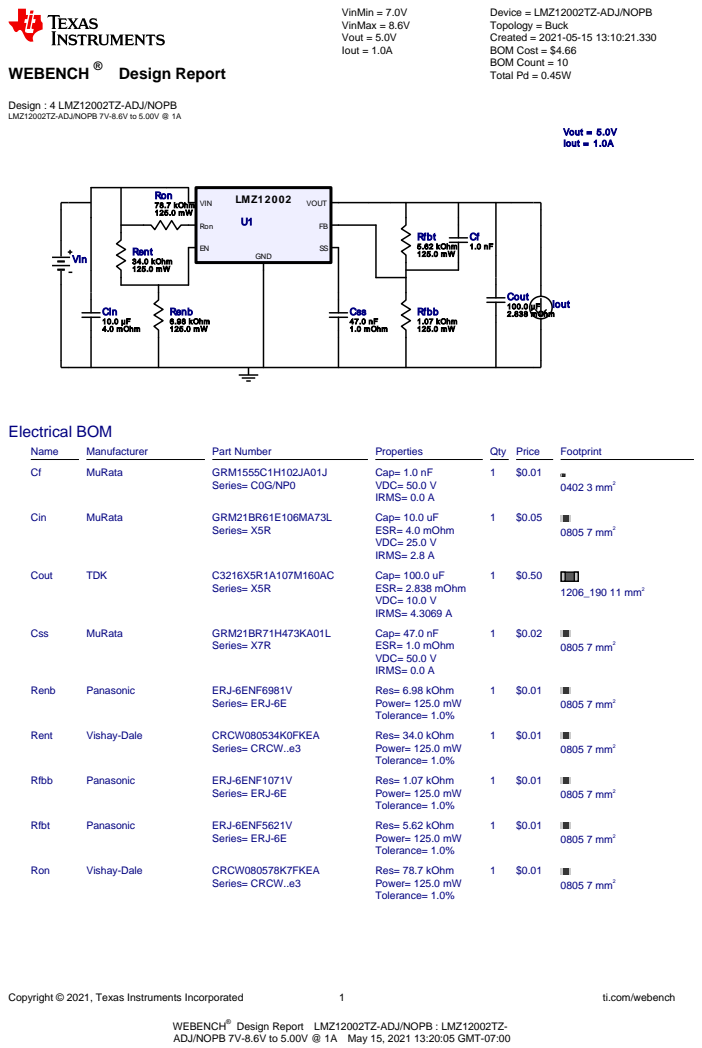
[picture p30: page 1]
Copyright © 2021, Texas Instruments Incorporated; ti.com/webench; VinMin = 7.0V VinMax = 8.6V Vout = 5.0V Iout = 1.0A; Cin 10.0 µF 4.0 mOhm; Cout; 100.0 µF Css; 2.838 mOhm; 47.0 nF 1.0 mOhm; Renb 6.98 kOhm 125.0 mW; Rent 34.0 kOhm 125.0 mW; Rfbb 1.07 kOhm 125.0 mW; Rfbt 5.62 kOhm 125.0 mW; Ron 78.7 kOhm 125.0 mW; LMZ12002 VIN; Ron; VOUT; SS GND; Vout = 5.0V Iout = 1.0A; Vin; Iout; Electrical BOM; Name; Manufacturer; Part Number; Properties; Qty Price; Footprint; MuRata; GRM1555C1H102JA01J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

Device = LMZ12002TZ-ADJ/NOPB
Topology = Buck
Created = 2021-05-15 13:10:21.330
BOM Cost = $4.66
BOM Count = 10
Total Pd = 0.45W

Design : 4 LMZ12002TZ-ADJ/NOPB
LMZ12002TZ-ADJ/NOPB 7V-8.6V to 5.00V @ 1A

WEBENCH®
ADJ/NOPB 7V-8.6V to 5.00V @ 1A May 15, 2021 13:20:05 GMT-07:00

Design Report LMZ12002TZ-ADJ/NOPB : LMZ12002TZ-

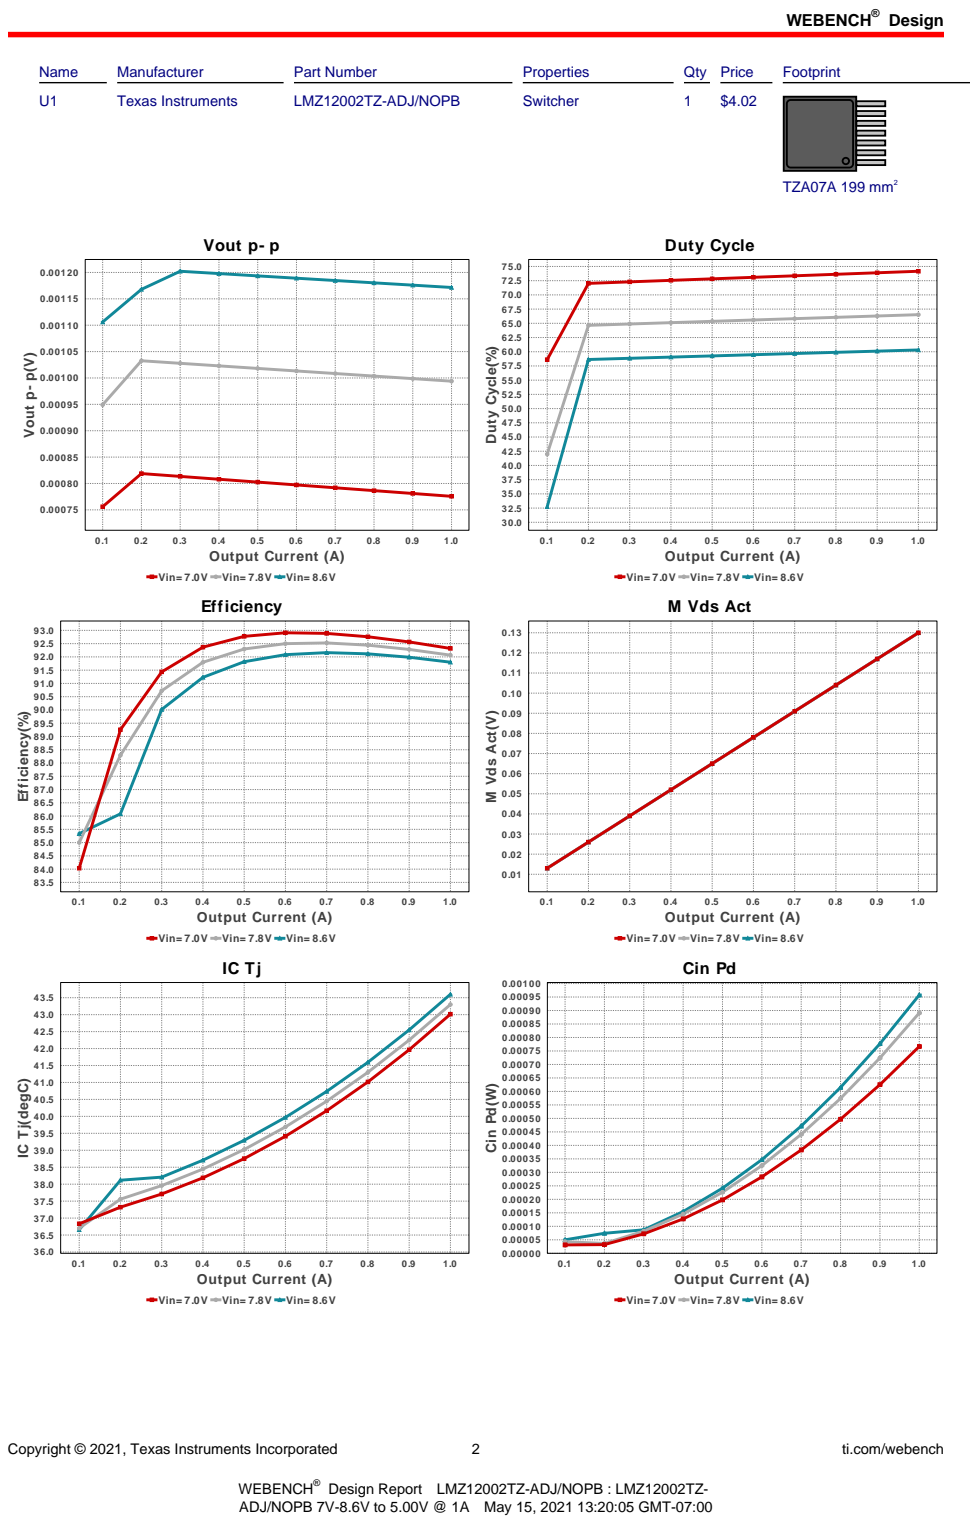
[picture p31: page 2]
Design; Copyright © 2021, Texas Instruments Incorporated; ti.com/webench; Name; Manufacturer; Part Number; Properties; Qty Price; Footprint; Texas Instruments; LMZ12002TZ-ADJ/NOPB; Switcher; TZA07A 199 mm²; Vout p- p; 1.0 Output Current (A); Vout p- p(V); Duty Cycle; Duty Cycle(%); Efficiency(%); M Vds Act(V); Cin Pd(W)

Vin= 7.0V Vin= 7.8V Vin= 8.6V
Efficiency

M Vds Act

Cin Pd

IC Tj(degC)

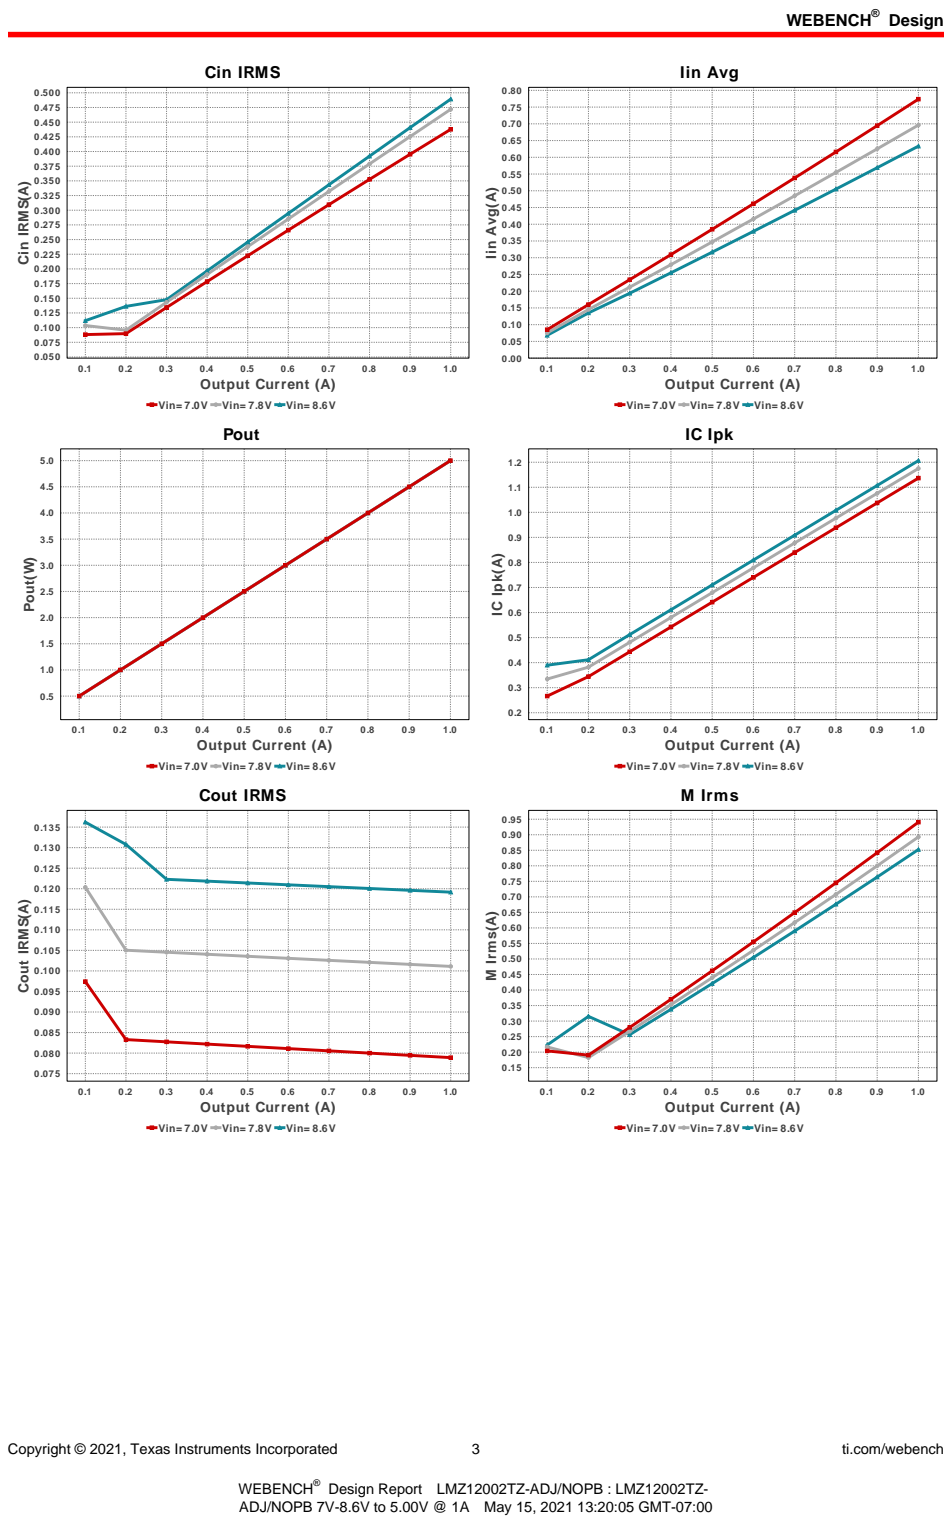
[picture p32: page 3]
Copyright © 2021, Texas Instruments Incorporated; ti.com/webench; Cin IRMS; 1.0 Output Current (A); Cin IRMS(A); Iin Avg; Iin Avg(A); Pout; Pout(W); IC Ipk; IC Ipk(A); Cout IRMS(A); M Irms(A)

Vin= 7.0V Vin= 7.8V Vin= 8.6V

Cout IRMS

M Irms

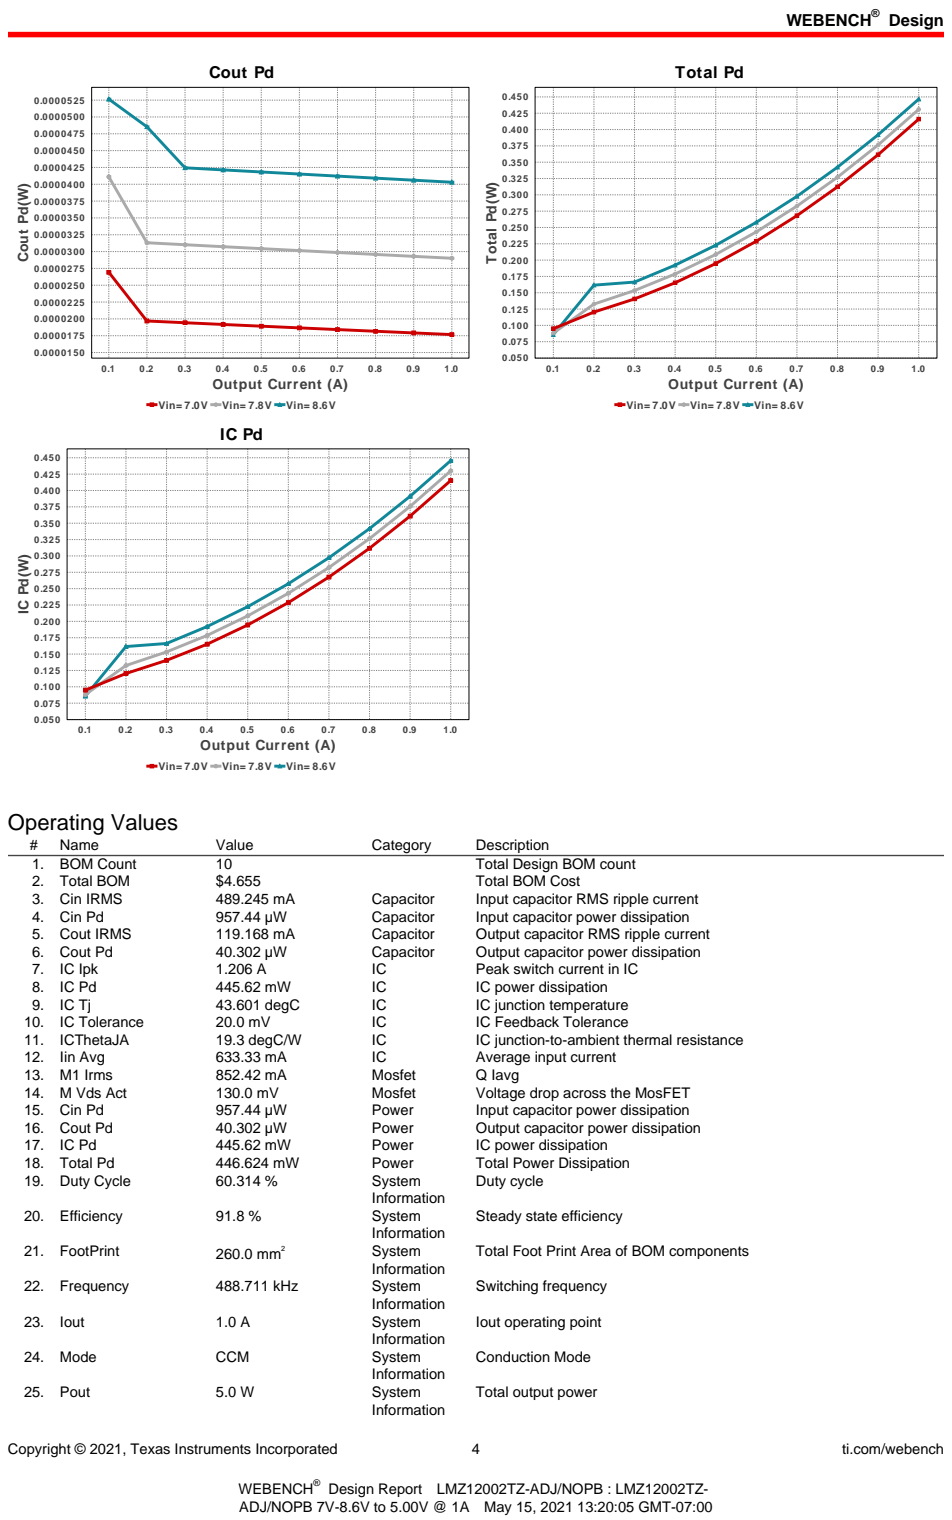
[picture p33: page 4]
Copyright © 2021, Texas Instruments Incorporated; ti.com/webench; Cout Pd; 1.0 Output Current (A); Cout Pd(W); Total Pd; Total Pd(W); Operating Values; Name; Value; Category; Description; 1. BOM Count; Total Design BOM count; 2. Total BOM; Total BOM Cost; 3. Cin IRMS; Capacitor; Input capacitor RMS ripple current; 4. Cin Pd; Input capacitor power dissipation; 5. Cout IRMS; Output capacitor RMS ripple current; 6. Cout Pd; Output capacitor power dissipation; 7. IC Ipk; Peak switch current in IC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

Vin= 7.0V Vin= 7.8V Vin= 8.6V

Steady state efficiency

Total Foot Print Area of BOM components

Iout operating point

Total output power

Copyright © 2021, Texas Instruments Incorporated | 5 | ti.com/webench
# | Name | Value | Category | Description

26. Vin | 8.6 V | System
| | | Information | Vin operating point
27. Vout | 5.0 V | System
| | | Information | Operational Output Voltage
28. Vout Actual | 5.002 V | System
| | | Information | Vout Actual calculated based on selected voltage divider resistors
29. Vout Tolerance | 4.24 % | System
| | | Information | Vout Tolerance based on IC Tolerance (no load) and voltage divider resistors if applicable
30. Vout p-p | 1.172 mV | System
| | | Information | Peak-to-peak output ripple voltage

## Design Inputs

Name | Value | Description
Iout | 1.0 | Maximum Output Current
SoftStart | 5.0 ms | Soft Start Time (ms)
VinMax | 8.6 | Maximum input voltage
VinMin | 7.0 | Minimum input voltage
Vout | 5.0 | Output Voltage
| base_pn | | LMZ12002 | Base Product Number
source | DC | Input Source Type
Ta | 35.0 | Ambient temperature


Copyright © 2021, Texas Instruments Incorporated | 6 | ti.com/webench

## Assembly

## Component Testing

Some published data on components in datasheets such as Capacitor ESR and Inductor DC resistance is based on conservative values that will guarantee that the components always exceed the specification. For design purposes it is usually better to work with typical values. Since this data is not always available it is a good practice to measure the Capacitance and ESR values of Cin and Cout, and the inductance and DC resistance of L1 before assembly of the board. Any large discrepancies in values should be electrically simulated in WEBENCH to check for instabilities and thermally simulated in WebTHERM to make sure critical temperatures are not exceeded.
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

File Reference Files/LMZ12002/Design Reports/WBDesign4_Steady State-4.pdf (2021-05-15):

## WEBENCH ® Design Report

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

Design : 4 LMZ12002TZ-ADJ/NOPB
LMZ12002TZ-ADJ/NOPB 7V-8.6V to 5.00V @ 1A

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

Design Report LMZ12002TZ-ADJ/NOPB : LMZ12002TZ-

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

Vin= 7.0V Vin= 7.8V Vin= 8.6V
Efficiency

M Vds Act

Cin Pd

IC Tj(degC)

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

Vin= 7.0V Vin= 7.8V Vin= 8.6V

Cout IRMS

M Irms

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

Vin= 7.0V Vin= 7.8V Vin= 8.6V

Steady state efficiency

Total Foot Print Area of BOM components

Iout operating point

Total output power

Copyright © 2021, Texas Instruments Incorporated | 5 | ti.com/webench
# | Name | Value | Category | Description

26. Vin | 8.6 V | System
| | | Information | Vin operating point
27. Vout | 5.0 V | System
| | | Information | Operational Output Voltage
28. Vout Actual | 5.002 V | System
| | | Information | Vout Actual calculated based on selected voltage divider resistors
29. Vout Tolerance | 4.24 % | System
| | | Information | Vout Tolerance based on IC Tolerance (no load) and voltage divider resistors if applicable
30. Vout p-p | 1.172 mV | System
| | | Information | Peak-to-peak output ripple voltage

## Design Inputs

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


Copyright © 2021, Texas Instruments Incorporated | 6 | ti.com/webench

## Assembly

## Component Testing

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

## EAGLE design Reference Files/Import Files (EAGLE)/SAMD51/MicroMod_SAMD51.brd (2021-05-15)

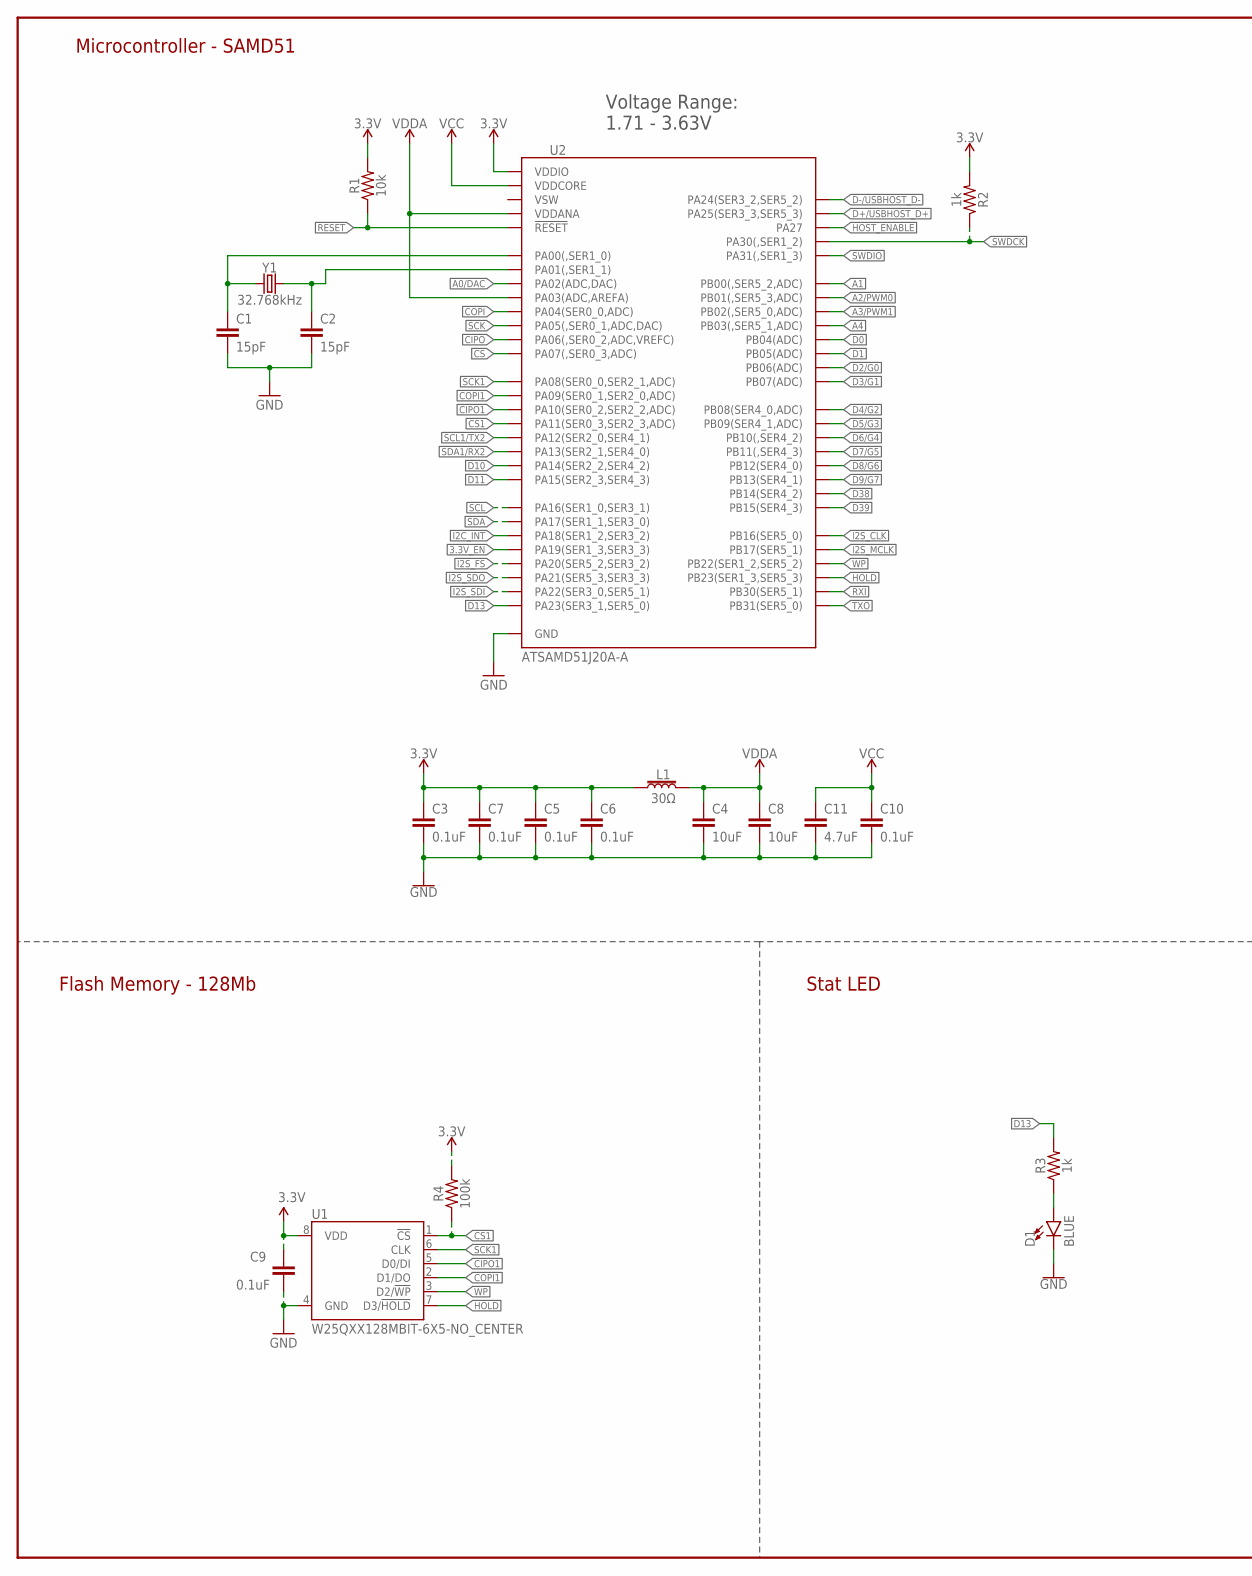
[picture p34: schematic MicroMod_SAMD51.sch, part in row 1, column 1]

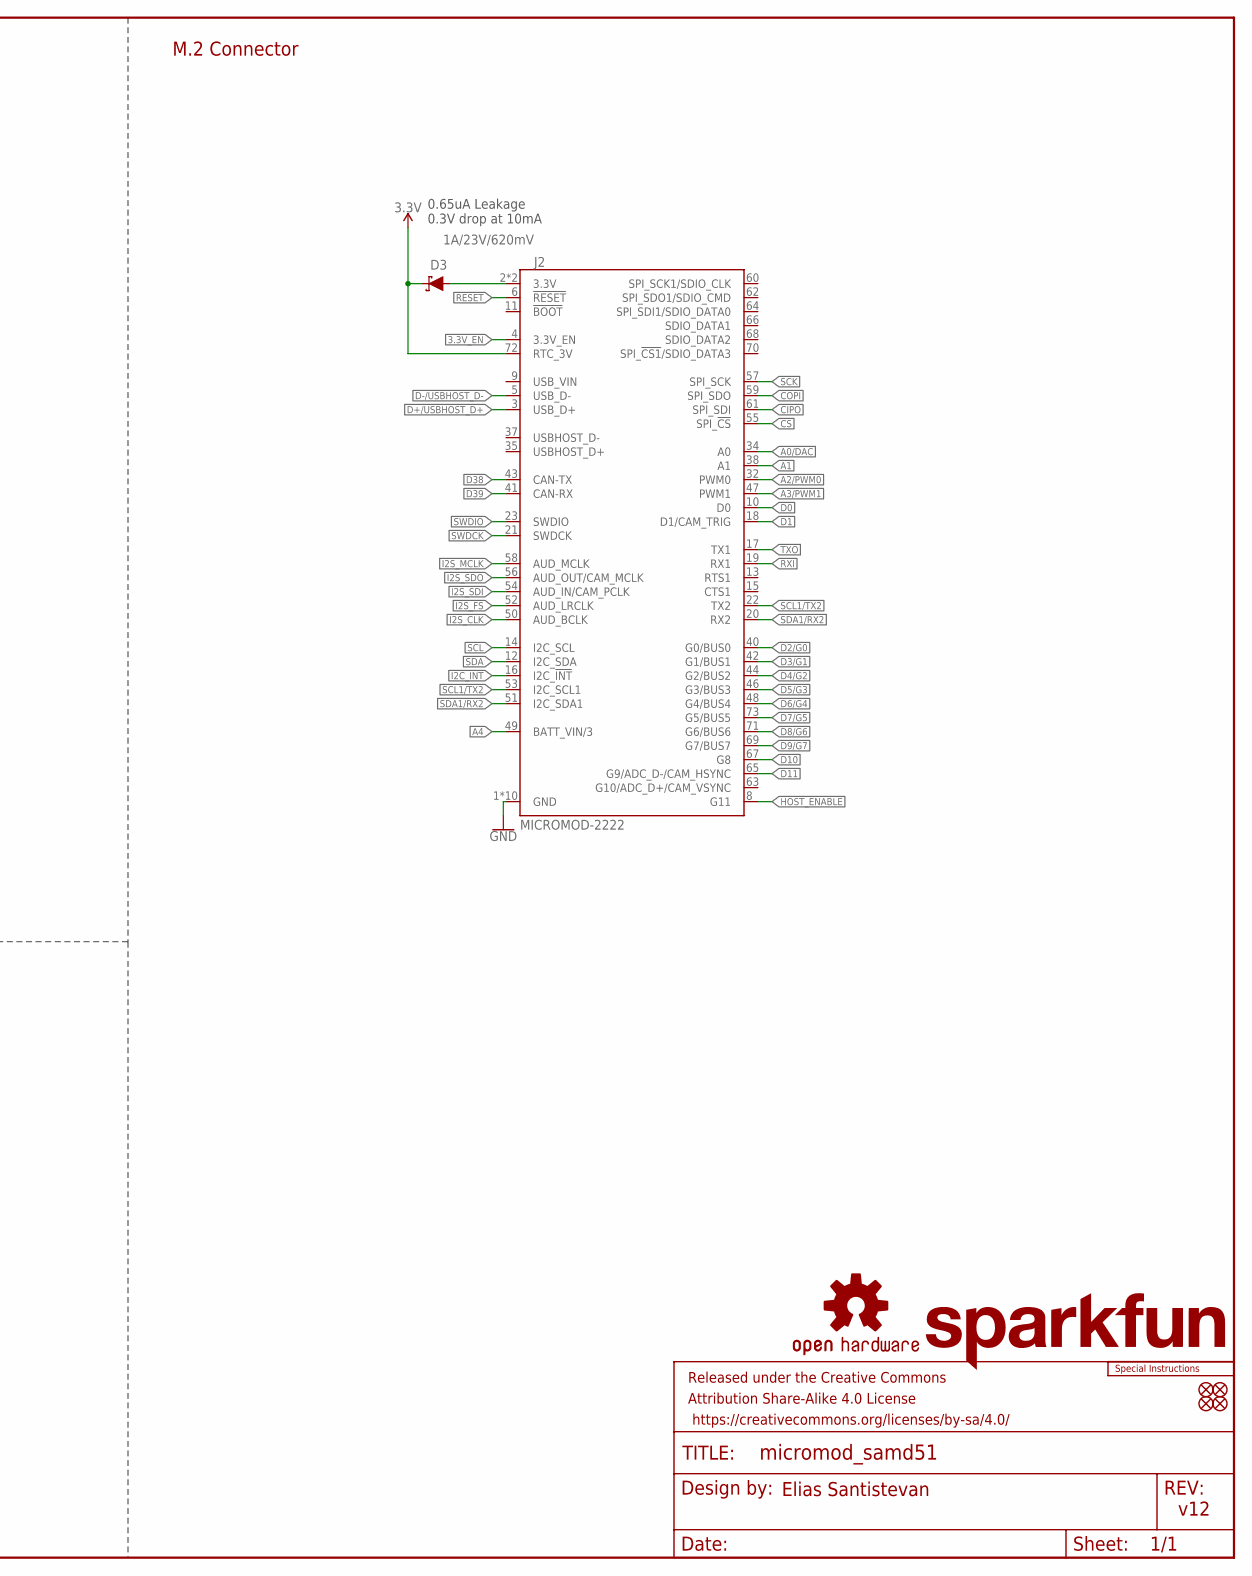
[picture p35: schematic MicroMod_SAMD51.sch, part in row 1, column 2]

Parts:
C1, C2: 15pF; 0402-TIGHT
C3, C5, C6, C7, C9, C10: 0.1uF; 0402-TIGHT
C4, C8: 10uF; 0402-TIGHT
C11: 4.7uF; 0402-TIGHT
D1: BLUE; LED-0603
D3: 1A/23V/620mV; SOD-323
FD5, FD6, FD7, FD8: FIDUCIALUFIDUCIAL; FIDUCIAL-MICRO
FRAME2: FRAME-LEDGER; CREATIVE_COMMONS
J2: MICROMOD-2222; M.2-CARD-E-22
L1: 30Ω; 0402-TIGHT
LOGO2: OSHW-LOGOMINI; OSHW-LOGO-MINI
LOGO5: SPECIAL_INSTRUCTIONS-ORDERING; ORDERING_INSTRUCTIONS
LOGO6: SFE_LOGO_NAME.1_INCH; SFE_LOGO_NAME_.1
R1: 10k; 0402-TIGHT
R2, R3: 1k; 0402-TIGHT
R4: 100k; 0402-TIGHT
U1: W25QXX128MBIT-6X5-NO_CENTER; WSON-8-6X5-NO_CENTERPAD
U2: ATSAMD51J20A-A; TQFP64
Y1: 32.768kHz; CRYSTAL-SMD-3.2X1.5MM

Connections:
3.3V: C3.1, C5.1, C6.1, C7.1, C9.1, D3.C, J2.72 (RTC_3V), L1.1, R1.2, R2.2, R4.2, U1.8 (VDD), U2.21 (VDDIO), U2.34 (VDDIO), U2.48 (VDDIO), U2.56 (VDDIO)
3.3V_EN: J2.4 (3.3V_EN), U2.38 (PA19(SER1_3,SER3_3))
3.3V_IN: D3.A, J2.2 (3.3V), J2.74 (3.3V)
!CS: J2.55 (SPI_!CS!), U2.16 (PA07(,SER0_3,ADC))
!CS1!: R4.1, U1.1 (!CS!), U2.20 (PA11(SER0_3,SER2_3,ADC))
!HOLD!: U1.7 (D3/!HOLD!), U2.50 (PB23(SER1_3,SER5_3))
!RESET: J2.6 (!RESET!), R1.1, U2.52 (!RESET)
!WP!: U1.3 (D2/!WP!), U2.49 (PB22(SER1_2,SER5_2))
A0/DAC: J2.34 (A0), U2.3 (PA02(ADC,DAC))
A1: J2.38 (A1), U2.61 (PB00(,SER5_2,ADC))
A2/PWM0: J2.32 (PWM0), U2.62 (PB01(,SER5_3,ADC))
A3/PWM1: J2.47 (PWM1), U2.63 (PB02(,SER5_0,ADC))
A4: J2.49 (BATT_VIN/3), U2.64 (PB03(,SER5_1,ADC))
CIPO: J2.61 (SPI_SDI), U2.15 (PA06(,SER0_2,ADC,VREFC))
CIPO1: U1.5 (D0/DI), U2.19 (PA10(SER0_2,SER2_2,ADC))
COPI: J2.59 (SPI_SDO), U2.13 (PA04(SER0_0,ADC))
COPI1: U1.2 (D1/DO), U2.18 (PA09(SER0_1,SER2_0,ADC))
D0: J2.10 (D0), U2.5 (PB04(ADC))
D1: J2.18 (D1/CAM_TRIG), U2.6 (PB05(ADC))
D2/G0: J2.40 (G0/BUS0), U2.9 (PB06(ADC))
D3/G1: J2.42 (G1/BUS1), U2.10 (PB07(ADC))
D4/G2: J2.44 (G2/BUS2), U2.11 (PB08(SER4_0,ADC))
D5/G3: J2.46 (G3/BUS3), U2.12 (PB09(SER4_1,ADC))
D6/G4: J2.48 (G4/BUS4), U2.23 (PB10(,SER4_2))
D7/G5: J2.73 (G5/BUS5), U2.24 (PB11(,SER4_3))
D8/G6: J2.71 (G6/BUS6), U2.25 (PB12(SER4_0))
D9/G7: J2.69 (G7/BUS7), U2.26 (PB13(SER4_1))
D10: J2.67 (G8), U2.31 (PA14(SER2_2,SER4_2))
D11: J2.65 (G9/ADC_D-/CAM_HSYNC), U2.32 (PA15(SER2_3,SER4_3))
D13: R3.2, U2.44 (PA23(SER3_1,SER5_0))
D38: J2.43 (CAN-TX), U2.27 (PB14(SER4_2))
D39: J2.41 (CAN-RX), U2.28 (PB15(SER4_3))
D+/USBHOST_D+: J2.3 (USB_D+), U2.46 (PA25(SER3_3,SER5_3))
D-/USBHOST_D-: J2.5 (USB_D-), U2.45 (PA24(SER3_2,SER5_2))
GND: C1.2, C2.2, C3.2, C4.2, C5.2, C6.2, C7.2, C8.2, C9.2, C10.2, C11.2, D1.C, J2.1 (GND), J2.7 (GND), J2.33 (GND), J2.36 (GND), J2.39 (GND), J2.45 (GND), J2.75 (GND), J2.GND1 (GND), J2.GND2 (GND), J2.GND3 (GND), U1.4 (GND), U2.7 (GND), U2.22 (GND), U2.33 (GND), U2.47 (GND), U2.54 (GND)
HOST_ENABLE: J2.8 (G11), U2.51 (PA27)
I2C_!INT!: J2.16 (I2C_!INT!), U2.37 (PA18(SER1_2,SER3_2))
I2S_CLK: J2.50 (AUD_BCLK), U2.39 (PB16(SER5_0))
I2S_FS: J2.52 (AUD_LRCLK), U2.41 (PA20(SER5_2,SER3_2))
I2S_MCLK: J2.58 (AUD_MCLK), U2.40 (PB17(SER5_1))
I2S_SDI: J2.54 (AUD_IN/CAM_PCLK), U2.43 (PA22(SER3_0,SER5_1))
I2S_SDO: J2.56 (AUD_OUT/CAM_MCLK), U2.42 (PA21(SER5_3,SER3_3))
unnamed: D1.A, R3.1
RXI: J2.19 (RX1), U2.59 (PB30(SER5_1))
SCK: J2.57 (SPI_SCK), U2.14 (PA05(,SER0_1,ADC,DAC))
SCK1: U1.6 (CLK), U2.17 (PA08(SER0_0,SER2_1,ADC))
SCL: J2.14 (I2C_SCL), U2.35 (PA16(SER1_0,SER3_1))
SCL1/TX2: J2.22 (TX2), J2.53 (I2C_SCL1), U2.29 (PA12(SER2_0,SER4_1))
SDA: J2.12 (I2C_SDA), U2.36 (PA17(SER1_1,SER3_0))
SDA1/RX2: J2.20 (RX2), J2.51 (I2C_SDA1), U2.30 (PA13(SER2_1,SER4_0))
SWDCK: J2.21 (SWDCK), R2.1, U2.57 (PA30(,SER1_2))
SWDIO: J2.23 (SWDIO), U2.58 (PA31(,SER1_3))
TXO: J2.17 (TX1), U2.60 (PB31(SER5_0))
VCC: C10.1, C11.1, U2.53 (VDDCORE)
VDDA: C4.1, C8.1, L1.2, U2.4 (PA03(ADC,AREFA)), U2.8 (VDDANA)
XIN32: C1.1, U2.1 (PA00(,SER1_0)), Y1.P$1 (1)
XOUT32: C2.1, U2.2 (PA01(,SER1_1)), Y1.P$2 (2)

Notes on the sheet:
v12
M.2 Connector
Microcontroller - SAMD51
Flash Memory - 128Mb
Stat LED
Elias Santistevan
0.65uA Leakage 0.3V drop at 10mA
Voltage Range: 1.71 - 3.63V

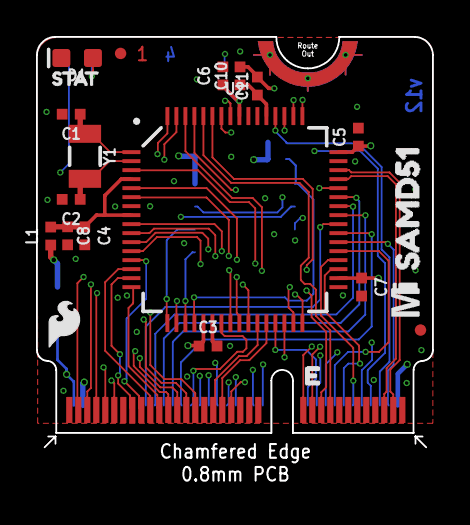
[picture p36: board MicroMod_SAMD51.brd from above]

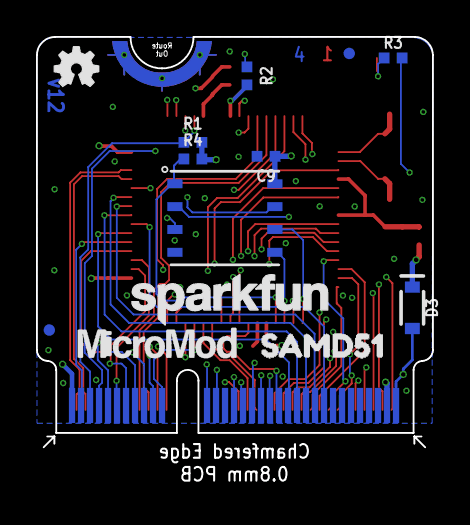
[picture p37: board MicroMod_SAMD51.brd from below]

Board: 4 copper layers, 22.0 x 22.8 mm, 36 parts (13 on the bottom side), 57 nets.

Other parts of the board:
U$1: MICROMOD_MI_LOGO_.35
U$4: MICROMOD_LOGO_.35
U$5, U$6: SAMD510
U$7: SFE_LOGO_FLAME_.1
U$8: STAT0

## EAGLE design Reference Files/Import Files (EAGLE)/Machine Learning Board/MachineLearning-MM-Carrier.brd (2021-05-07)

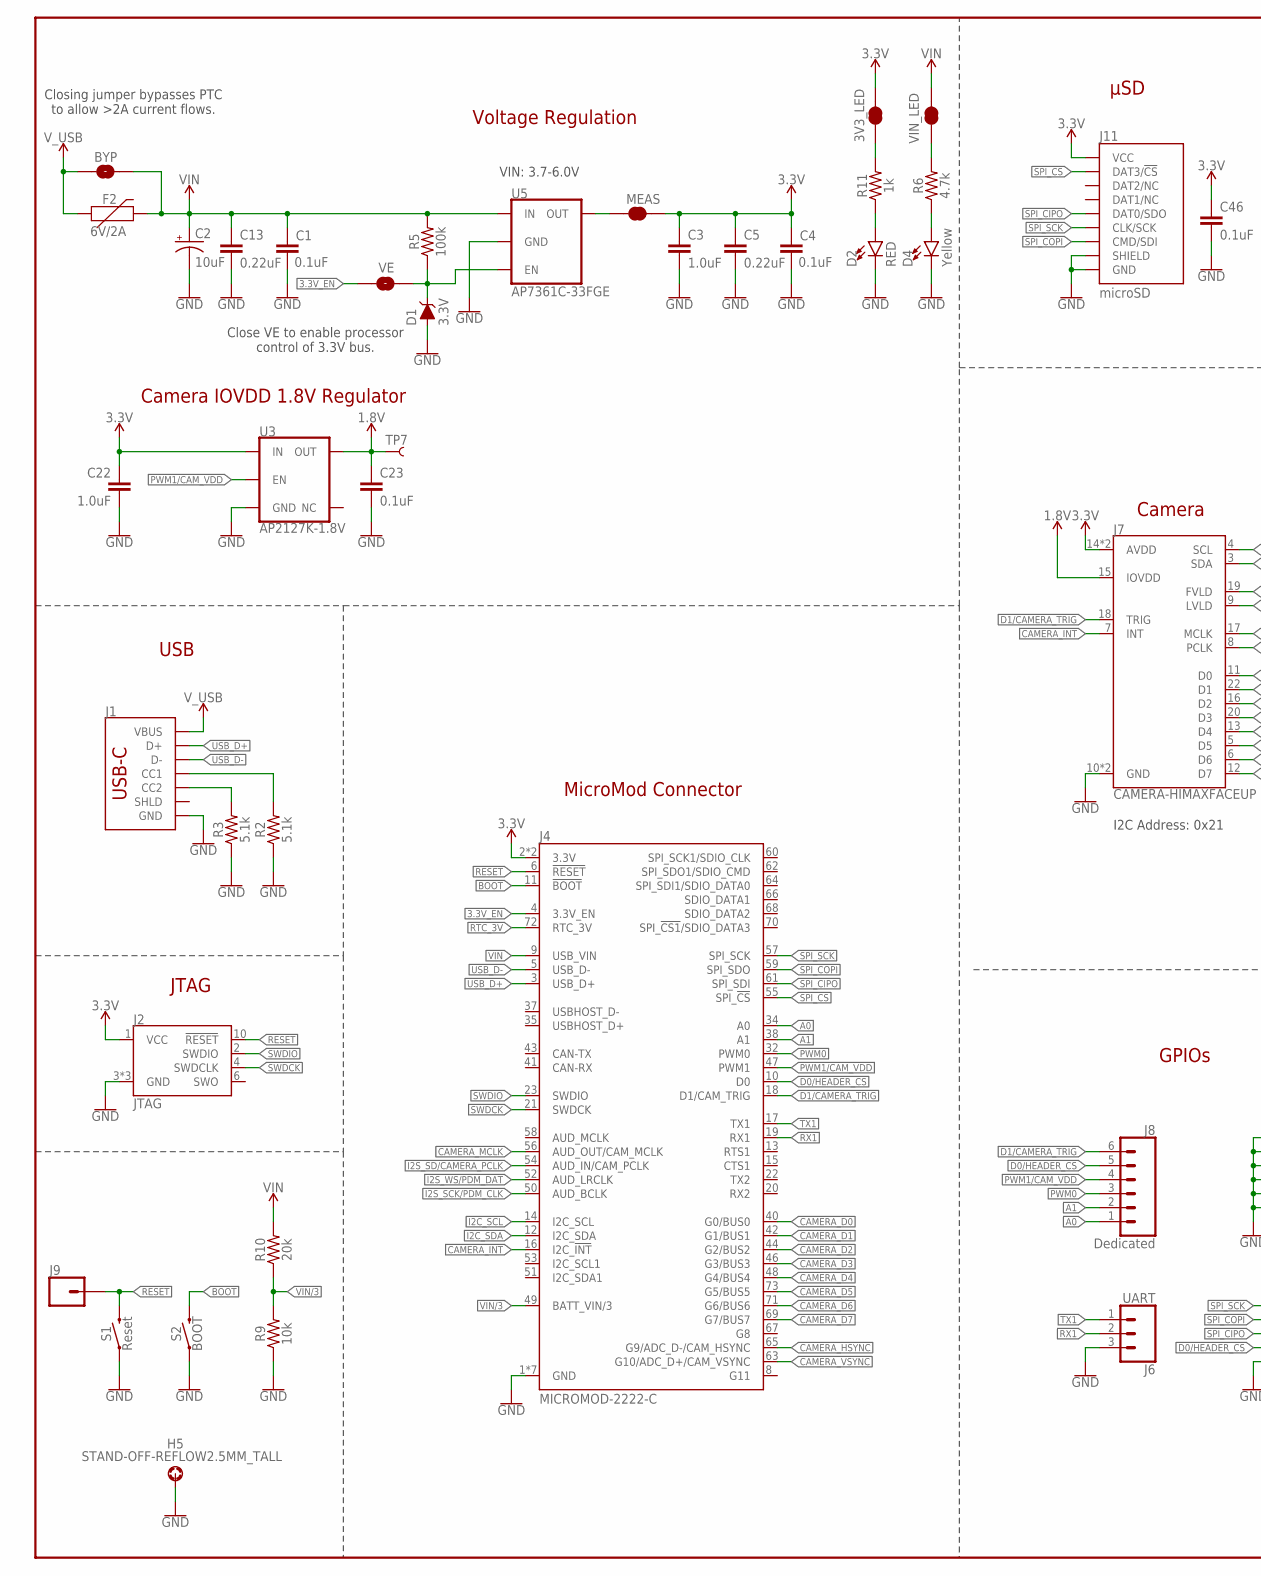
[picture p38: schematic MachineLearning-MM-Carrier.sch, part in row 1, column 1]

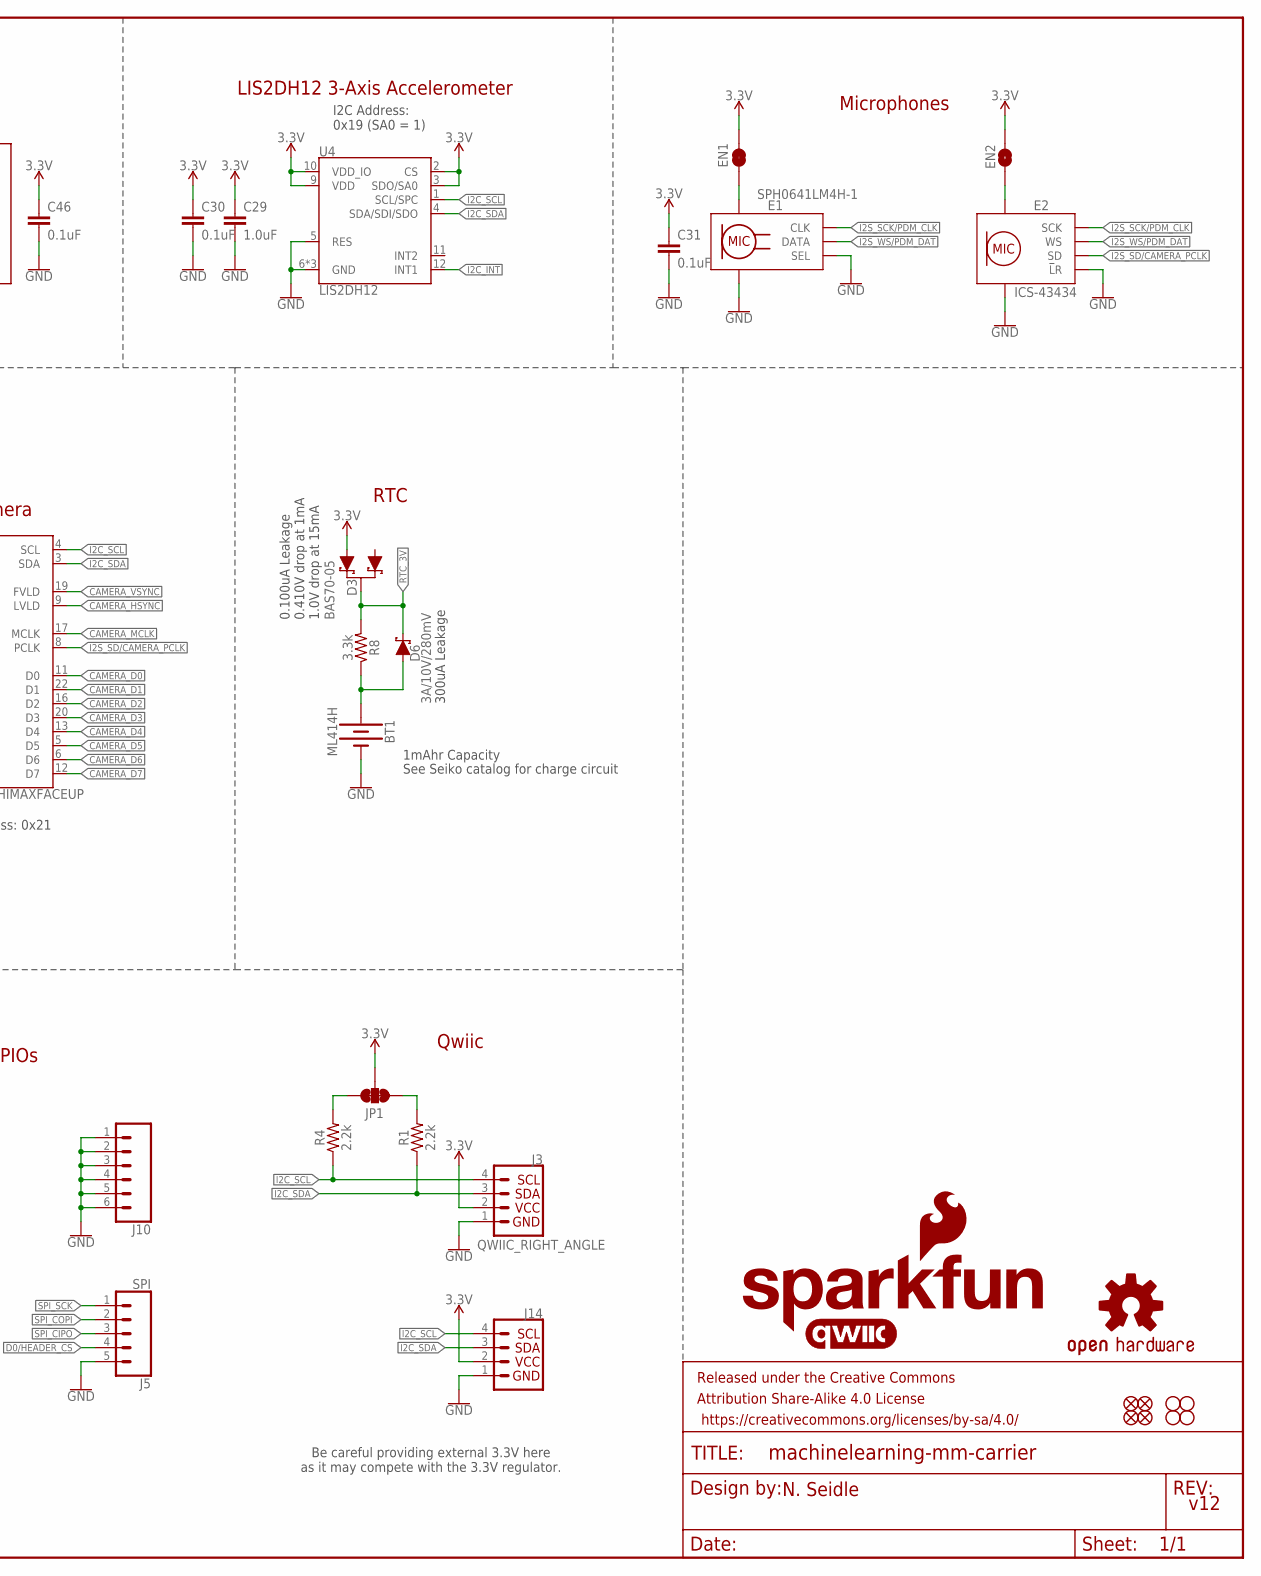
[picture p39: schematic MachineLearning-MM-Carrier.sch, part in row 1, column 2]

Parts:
3V3_LED: JUMPER-SMT_2_NC_TRACE_SILK; SMT-JUMPER_2_NC_TRACE_SILK
BT1: ML414H; ML414H_IV01E
BYP: JUMPER-SMT_2_NO_SILK; SMT-JUMPER_2_NO_SILK
C1, C4, C23, C30, C31, C46: 0.1uF; 0603
C2: 10uF; EIA3216
C3, C22, C29: 1.0uF; 0603
C5, C13: 0.22uF; 0603
D1: 3.3V; SOD-323
D2: RED; LED-0603
D3: BAS70-05; SOT23-3
D4: Yellow; LED-0603
D6: 3A/10V/280mV; SOD-323
E1: SPH0641LM4H-1; SPH0641LM4H-1_MICROPHONE
E2: ICS-43434
EN1: JUMPER-SMT_2_NC_TRACE_SILK; SMT-JUMPER_2_NC_TRACE_SILK
EN2: JUMPER-SMT_2_NO_SILK; SMT-JUMPER_2_NO_SILK
F2: 6V/2A; 1210
FD1, FD2, FD3, FD4: FIDUCIALUFIDUCIAL; FIDUCIAL-MICRO
FRAME1: FRAME-LEDGER; CREATIVE_COMMONS
H1, H2, H3, H4: STAND-OFF
H5: STAND-OFF-REFLOW2.5MM_TALL; STAND-OFF-REFLOW-M2.5
J1: USB_C_2-LAYER_PADS; USB-C-16P-2LAYER-PADS
J2: JTAG; 2X5-PTH-1.27MM
J3: QWIIC_RIGHT_ANGLE; JST04_1MM_RA
J4: MICROMOD-2222-C; M.2-CONNECTOR-E
J5: SPI; 1X05_NO_SILK
J6: UART; 1X03_NO_SILK
J7: CAMERA-HIMAXFACEUP; FPC05024-42201
J8: Dedicated; 1X06_NO_SILK
J9: CONN_01PTH_NO_SILK_YES_STOP; 1X01_NO_SILK
J10: CONN_06NO_SILK_NO_POP; 1X06_NO_SILK
J11: microSD; MICRO-SD-SOCKET
J14: I2C_STANDARD_NO_SILK; 1X04_NO_SILK
JP1: JUMPER-SMT_3_2-NC_TRACE_SILK; SMT-JUMPER_3_2-NC_TRACE_SILK
LOGO1: SFE_LOGO_NAME_FLAME.1_INCH; SFE_LOGO_NAME_FLAME_.1
LOGO2: QWIIC_LOGO_CONNECTOR; QWIIC_5.5MM
LOGO3: OSHW-LOGOMINI; OSHW-LOGO-MINI
MEAS: JUMPER-COMBO_2_NC_TRACE; COMBO-JUMPER_2_NC_TRACE
R1, R4: 2.2k; 0603
R2, R3: 5.1k; 0603
R5: 100k; 0603
R6: 4.7k; 0603
R8: 3.3k; 0603
R9: 10k; 0603
R10: 20k; 0603
R11: 1k; 0603
S1: Reset; TACTILE_SWITCH_SMD_5.2MM
S2: BOOT; TACTILE_SWITCH_SMD_5.2MM
TP7: TEST-POINT3X5; PAD.03X.05
U3: AP2127K-1.8V; SOT23-5
U4: LIS2DH12; LGA-12-LISDH12
U5: AP7361C-33FGE; UDFN-8
VE: JUMPER-SMT_2_NO_SILK; SMT-JUMPER_2_NO_SILK
VIN_LED: JUMPER-SMT_2_NC_TRACE_SILK; SMT-JUMPER_2_NC_TRACE_SILK

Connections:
1.8V: C23.1, J7.15 (IOVDD), TP7.P$1, U3.5 (OUT)
3.3V: 3V3_LED.2, C3.1, C4.1, C5.1, C22.1, C29.1, C30.1, C31.1, C46.1, D3.2 (A1), EN1.2, EN2.2, J2.1 (VCC), J3.2, J4.2 (3.3V), J4.74 (3.3V), J7.14 (AVDD), J7.21 (AVDD), J11.VCC, J14.2, JP1.2, MEAS.2, MEAS.4 (2), U3.1 (IN), U4.2 (CS), U4.3 (SDO/SA0), U4.9 (VDD), U4.10 (VDD_IO)
3.3V_EN: J4.4 (3.3V_EN), VE.1
!BOOT!: J4.11 (!BOOT!), S2.3 (2), S2.4 (2)
!RESET!: J2.10 (!RESET), J4.6 (!RESET!), J9.1, S1.3 (2), S1.4 (2)
A0: J4.34 (A0), J8.1
A1: J4.38 (A1), J8.2
CAMERA_D0: J4.40 (G0/BUS0), J7.11 (D0)
CAMERA_D1: J4.42 (G1/BUS1), J7.22 (D1)
CAMERA_D2: J4.44 (G2/BUS2), J7.16 (D2)
CAMERA_D3: J4.46 (G3/BUS3), J7.20 (D3)
CAMERA_D4: J4.48 (G4/BUS4), J7.13 (D4)
CAMERA_D5: J4.73 (G5/BUS5), J7.5 (D5)
CAMERA_D6: J4.71 (G6/BUS6), J7.6 (D6)
CAMERA_D7: J4.69 (G7/BUS7), J7.12 (D7)
CAMERA_HSYNC: J4.65 (G9/ADC_D-/CAM_HSYNC), J7.9 (LVLD)
CAMERA_INT: J4.16 (I2C_!INT!), J7.7 (INT)
CAMERA_MCLK: J4.56 (AUD_OUT/CAM_MCLK), J7.17 (MCLK)
CAMERA_VSYNC: J4.63 (G10/ADC_D+/CAM_VSYNC), J7.19 (FVLD)
D0/HEADER_!CS!: J4.10 (D0), J5.4, J8.5
D1/CAMERA_TRIG: J4.18 (D1/CAM_TRIG), J7.18 (TRIG), J8.6
GND: BT1.-, C1.2, C2.-, C3.2, C4.2, C5.2, C13.2, C22.2, C23.2, C29.2, C30.2, C31.2, C46.2, D1.A, D2.C, D4.C, E1.2 (SEL), E1.3 (GND), E1.6 (GND), E1.7 (GND), E1.8 (GND), E2.2 (!L!R), E2.3 (GND), E2.7 (GND), E2.8 (GND), E2.9 (GND), H5.1, J1.GND, J1.GND2 (GND), J2.3 (GND), J2.5 (GND), J2.9 (GND), J3.1, J4.1 (GND), J4.7 (GND), J4.33 (GND), J4.36 (GND), J4.39 (GND), J4.45 (GND), J4.75 (GND), J5.5, J6.3, J7.10 (GND), J7.23 (GND), J10.1, J10.2, J10.3, J10.4, J10.5, J10.6, J11.CD1 (SHIELD), J11.GND, J11.GND1 (GND), J11.GND3 (GND), J14.1, R2.1, R3.1, R9.1, S1.1, S1.2 (1), S2.1, S2.2 (1), U3.2 (GND), U4.5 (RES), U4.6 (GND), U4.7 (GND), U4.8 (GND), U5.4 (GND), U5.EP (GND)
I2C_!INT!: U4.12 (INT1)
I2C_SCL: J3.4, J4.14 (I2C_SCL), J7.4 (SCL), J14.4, R4.1, U4.1 (SCL/SPC)
I2C_SDA: J3.3, J4.12 (I2C_SDA), J7.3 (SDA), J14.3, R1.1, U4.4 (SDA/SDI/SDO)
I2S_SCK/PDM_CLK: E1.4 (CLK), E2.4 (SCK), J4.50 (AUD_BCLK)
I2S_SD/CAMERA_PCLK: E2.6 (SD), J4.54 (AUD_IN/CAM_PCLK), J7.8 (PCLK)
I2S_WS/PDM_DAT: E1.1 (DATA), E2.1 (WS), J4.52 (AUD_LRCLK)
unnamed: R6.2, VIN_LED.1
unnamed: JP1.3, R4.2
unnamed: JP1.1, R1.2
unnamed: E1.5 (VDD), EN1.1
unnamed: E2.5 (VDD), EN2.1
unnamed: 3V3_LED.1, R11.2
unnamed: D2.A, R11.1
unnamed: D4.A, R6.1
unnamed: J1.A5 (CC1), R2.2
unnamed: J1.B5 (CC2), R3.2
unnamed: D1.C, R5.1, U5.5 (EN), VE.2
unnamed: BT1.+, D6.A, R8.1
PWM0: J4.32 (PWM0), J8.3
PWM1/CAM_VDD: J4.47 (PWM1), J8.4, U3.3 (EN)
RTC_3V: D3.3 (C), D6.C, J4.72 (RTC_3V), R8.2
RX1: J4.19 (RX1), J6.2
SPI_!CS!: J4.55 (SPI_!CS!), J11.CS/DAT3 (DAT3/!CS!)
SPI_CIPO: J4.61 (SPI_SDI), J5.3, J11.DO/DAT0 (DAT0/SDO)
SPI_COPI: J4.59 (SPI_SDO), J5.2, J11.DI/CMD (CMD/SDI)
SPI_SCK: J4.57 (SPI_SCK), J5.1, J11.SCLK (CLK/SCK)
SWDCK: J2.4 (SWDCLK), J4.21 (SWDCK)
SWDIO: J2.2 (SWDIO), J4.23 (SWDIO)
TX1: J4.17 (TX1), J6.1
USB_D+: J1.A6 (D+), J1.B6 (D+), J4.3 (USB_D+)
USB_D-: J1.A7 (D-), J1.B7 (D-), J4.5 (USB_D-)
VIN: BYP.2, C1.1, C2.+, C13.1, F2.2, J4.9 (USB_VIN), R5.2, R10.2, U5.8 (IN), VIN_LED.2
VIN/3: J4.49 (BATT_VIN/3), R9.2, R10.1
VREG_3.3V: MEAS.1, MEAS.3 (1), U5.1 (OUT)
V_USB: BYP.1, F2.1, J1.VBUS1 (VBUS), J1.VBUS2 (VBUS)

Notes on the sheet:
LIS2DH12 3-Axis Accelerometer
I2C Address: 0x19 (SA0 = 1)
I2C Address: 0x21
μSD
300uA Leakage
See Seiko catalog for charge circuit
1mAhr Capacity
Closing jumper bypasses PTC to allow >2A current flows.
JTAG
Camera IOVDD 1.8V Regulator
USB
GPIOs
Camera
Microphones
Qwiic
RTC
Voltage Regulation
MicroMod Connector
0.100uA Leakage 0.410V drop at 1mA 1.0V drop at 15mA
N. Seidle
v12
VIN: 3.7-6.0V
Be careful providing external 3.3V here as it may compete with the 3.3V regulator.
Close VE to enable processor control of 3.3V bus.

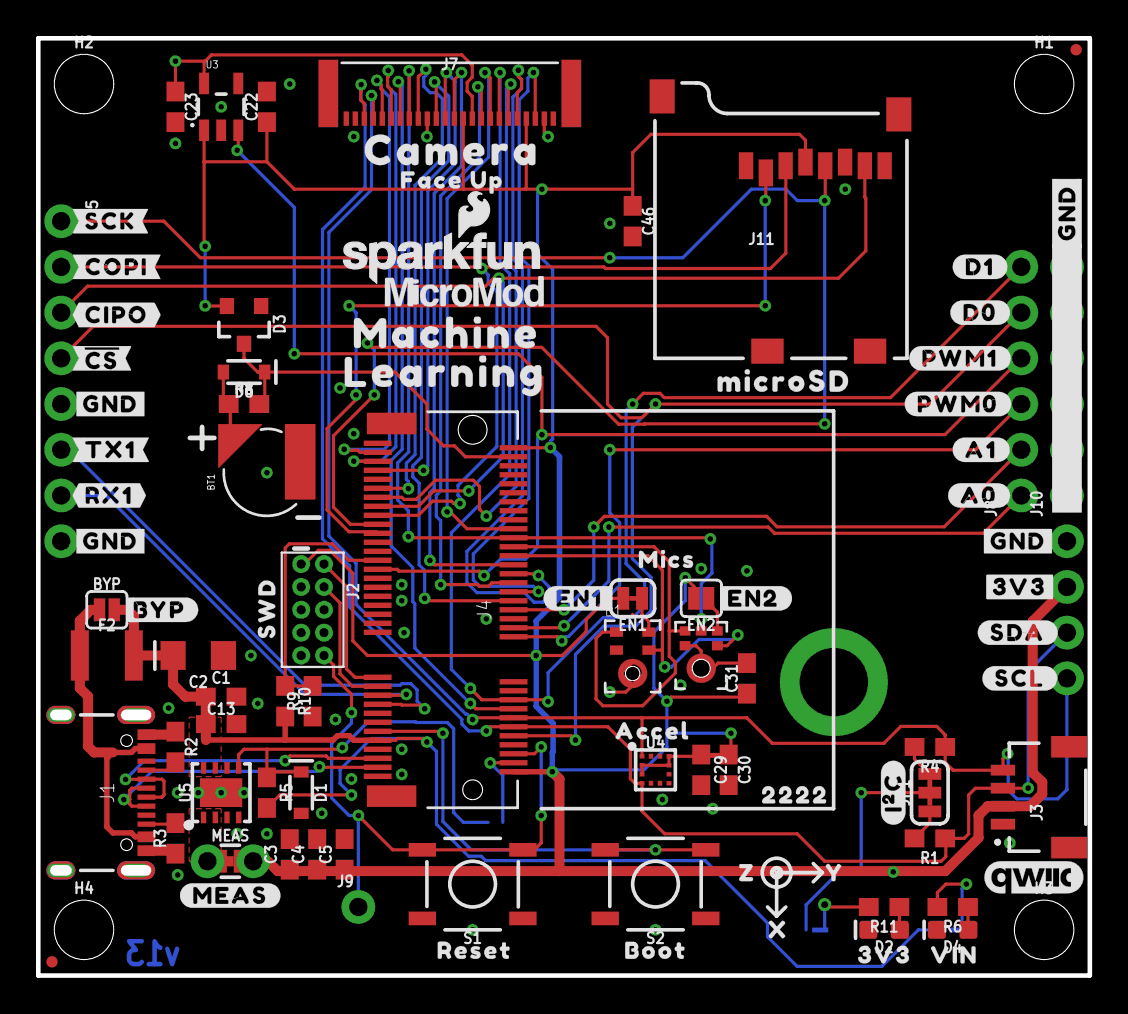
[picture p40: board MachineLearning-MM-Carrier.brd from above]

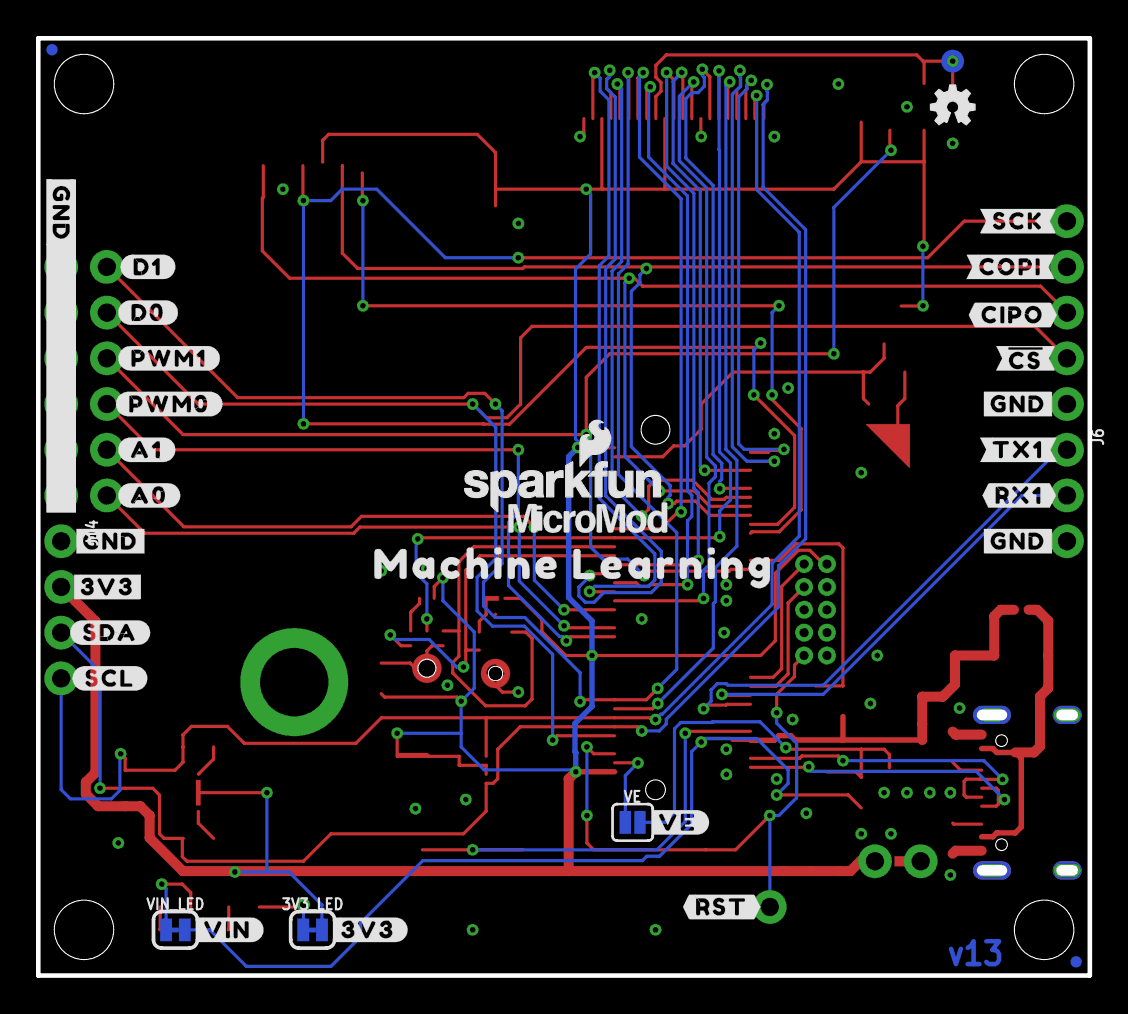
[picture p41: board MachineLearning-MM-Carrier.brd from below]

Board: 2 copper layers, 58.4 x 52.1 mm, 138 parts (36 on the bottom side), 56 nets.

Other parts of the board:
LOGO4: SFE_LOGO_NAME_FLAME.1_INCH; SFE_LOGO_NAME_FLAME_.1
U$1: #EN1#3
U$2: #EN2#4
U$3: CAMERA0
U$4: #3V3#0
U$5: MICS0
U$6, U$7: #A0#5
U$8, U$9: #A1#4
U$10, U$25: #D0#1
U$11, U$12, U$15, U$16: #GND#0
U$13, U$14: #3V3#1
U$17: #RST#1
U$18: #VE#0
U$19: #MEAS#2
U$20: #VIN#1
U$21: SWD0
U$22: FACE_UP0
U$23: #I�C#0
U$24, U$34: MICROMOD_LOGO_.35
U$26, U$37: MACHINE0
U$27, U$30: LEARNING1
U$28: MICROSD0
U$29, U$31: #D1#0
U$32, U$41: #PWM0#3
U$33: #BYP#1
U$35, U$68: ##CS##3
U$36: 3V37
U$38: 22223
U$39: ACCEL4
U$40: BOOT5
U$42, U$49: #PWM1#2
U$43, U$44: #SCL#3
U$45: RESET6
U$46: VIN8
U$47: X1
U$48: Y2
U$50, U$51: #SDA#2
U$52: Z0
U$69, U$70: #CIPO#2
U$71, U$72: #COPI#1
U$73, U$74, U$81, U$82: #GND#4
U$75, U$76: #RX1#6
U$77, U$78: #SCK#0
U$79, U$80: #TX1#5

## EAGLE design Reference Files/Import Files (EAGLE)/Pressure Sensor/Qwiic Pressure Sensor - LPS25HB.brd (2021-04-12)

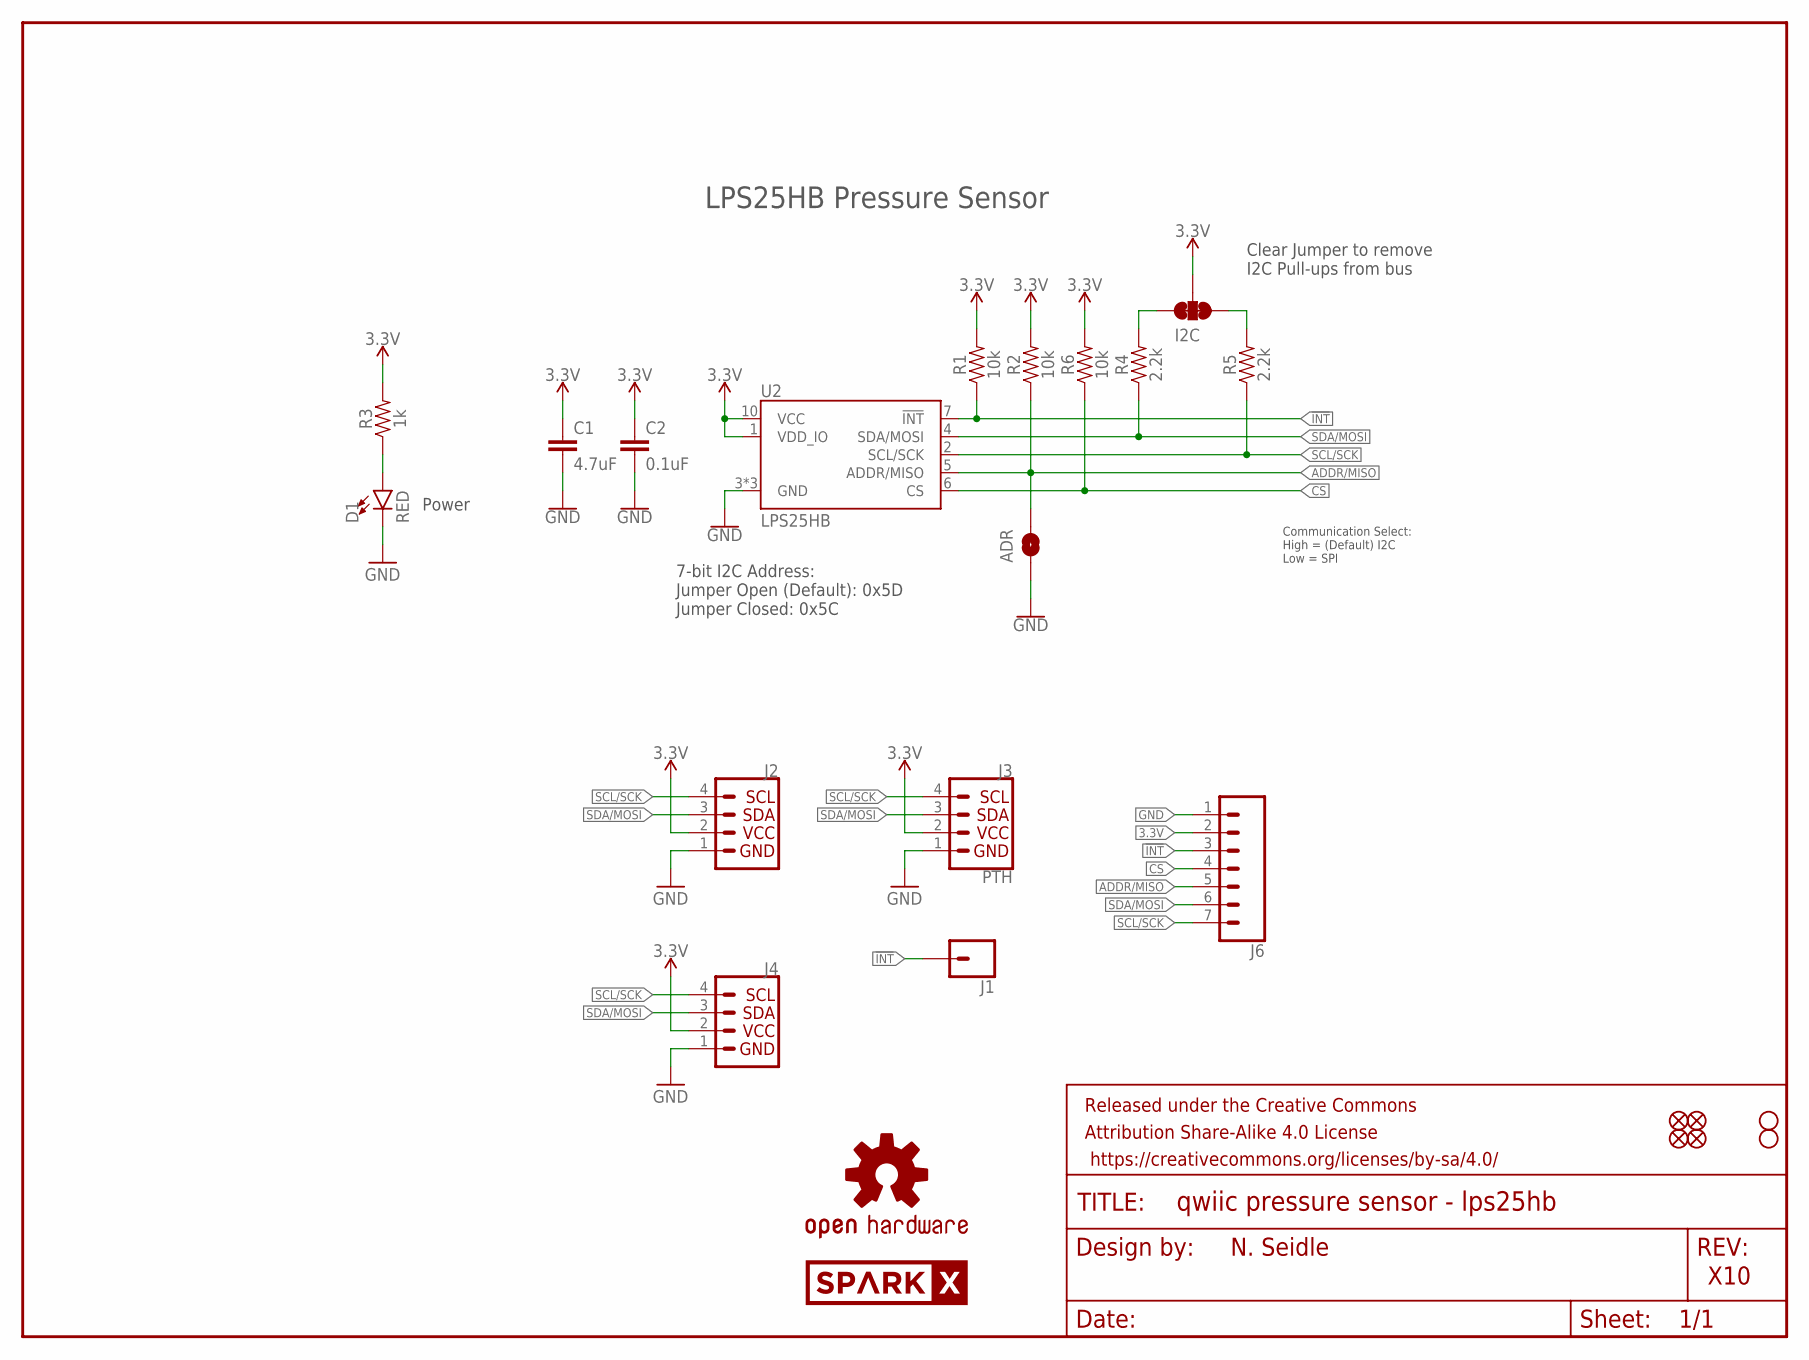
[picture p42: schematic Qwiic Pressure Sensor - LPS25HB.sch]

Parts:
ADR: JUMPER-SMT_2_NO_SILK; SMT-JUMPER_2_NO_SILK
C1: 4.7uF; 0603
C2: 0.1uF; 0603
D1: RED; LED-0603
FRAME1: FRAME-LETTER; CREATIVE_COMMONS
I2C: JUMPER-SMT_3_2-NC_TRACE_SILK; SMT-JUMPER_3_2-NC_TRACE_SILK
J1: CONN_01PTH_NO_SILK_YES_STOP; 1X01_NO_SILK
J2, J4: I2C_STANDARDQWIIC; 1X04_1MM_RA
J3: PTH; 1X04_NO_SILK
J6: CONN_07NO_SILK; 1X07_NO_SILK
JP1, JP2, JP5, JP6: FIDUCIALUFIDUCIAL; MICRO-FIDUCIAL
JP3, JP4: STAND-OFF
LOGO1: OSHW-LOGOMINI; OSHW-LOGO-MINI
R1, R2, R6: 10k; 0603
R3: 1k; 0603
R4, R5: 2.2k; 0603
U2: LPS25HB
U$2: SPARKX-LOGO4; SPARKX-MEDIUM

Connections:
3.3V: C1.1, C2.1, I2C.2, J2.2, J3.2 (VCC), J4.2, J6.2, R1.2, R2.2, R3.2, R6.2, U2.1 (VDD_IO), U2.10 (VCC)
!INT: J1.1, J6.3, R1.1, U2.7 (!INT)
ADDR/MISO: ADR.2, J6.5, R2.1, U2.5 (ADDR/MISO)
CS: J6.4, R6.1, U2.6 (CS)
GND: ADR.1, C1.2, C2.2, D1.C, J2.1, J3.1 (GND), J4.1, J6.1, U2.3 (GND), U2.8 (GND), U2.9 (GND)
unnamed: I2C.1, R5.2
unnamed: I2C.3, R4.2
unnamed: D1.A, R3.1
SCL/SCK: J2.4, J3.4 (SCL), J4.4, J6.7, R5.1, U2.2 (SCL/SCK)
SDA/MOSI: J2.3, J3.3 (SDA), J4.3, J6.6, R4.1, U2.4 (SDA/MOSI)

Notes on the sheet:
N. Seidle
X10
Clear Jumper to remove I2C Pull-ups from bus
Power
LPS25HB Pressure Sensor
7-bit I2C Address: Jumper Open (Default): 0x5D Jumper Closed: 0x5C
Communication Select: High = (Default) I2C Low = SPI

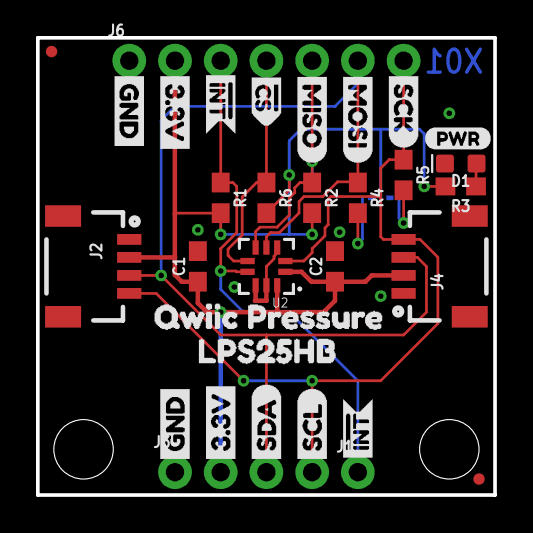
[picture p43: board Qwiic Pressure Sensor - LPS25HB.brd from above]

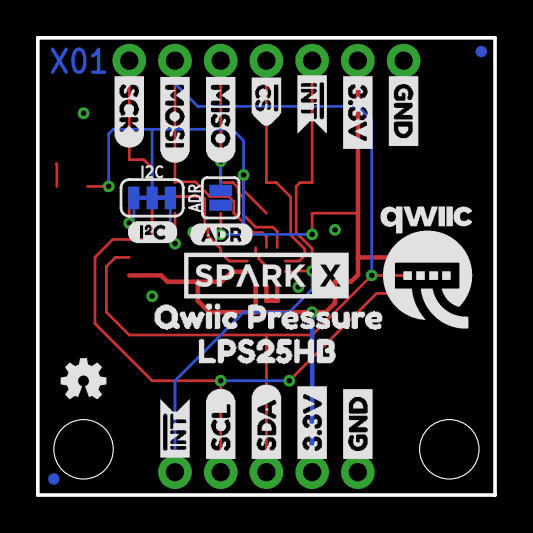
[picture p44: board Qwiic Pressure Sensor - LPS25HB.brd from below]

Board: 2 copper layers, 25.4 x 25.4 mm, 58 parts (23 on the bottom side), 10 nets.

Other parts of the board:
U$1, U$37: QWIIC_PRESSURE1
U$3, U$22, U$31, U$32: GND1
U$4, U$21, U$30, U$33: 3#3V2
U$5, U$27: SDA8
U$6, U$26: SCL9
U$7, U$35: LPS25HB0
U$9: QWIIC-LOGO-MEDIUM
U$10, U$11: MISO
U$12: I_SUPER2_C-()-03
U$15: PWR-()-03
U$16, U$17: MOSI
U$18, U$19: SCK-[)
U$20, U$23: CS#-[>
U$24, U$25, U$28, U$29: INT#-[<
U$34: ADR-()-03

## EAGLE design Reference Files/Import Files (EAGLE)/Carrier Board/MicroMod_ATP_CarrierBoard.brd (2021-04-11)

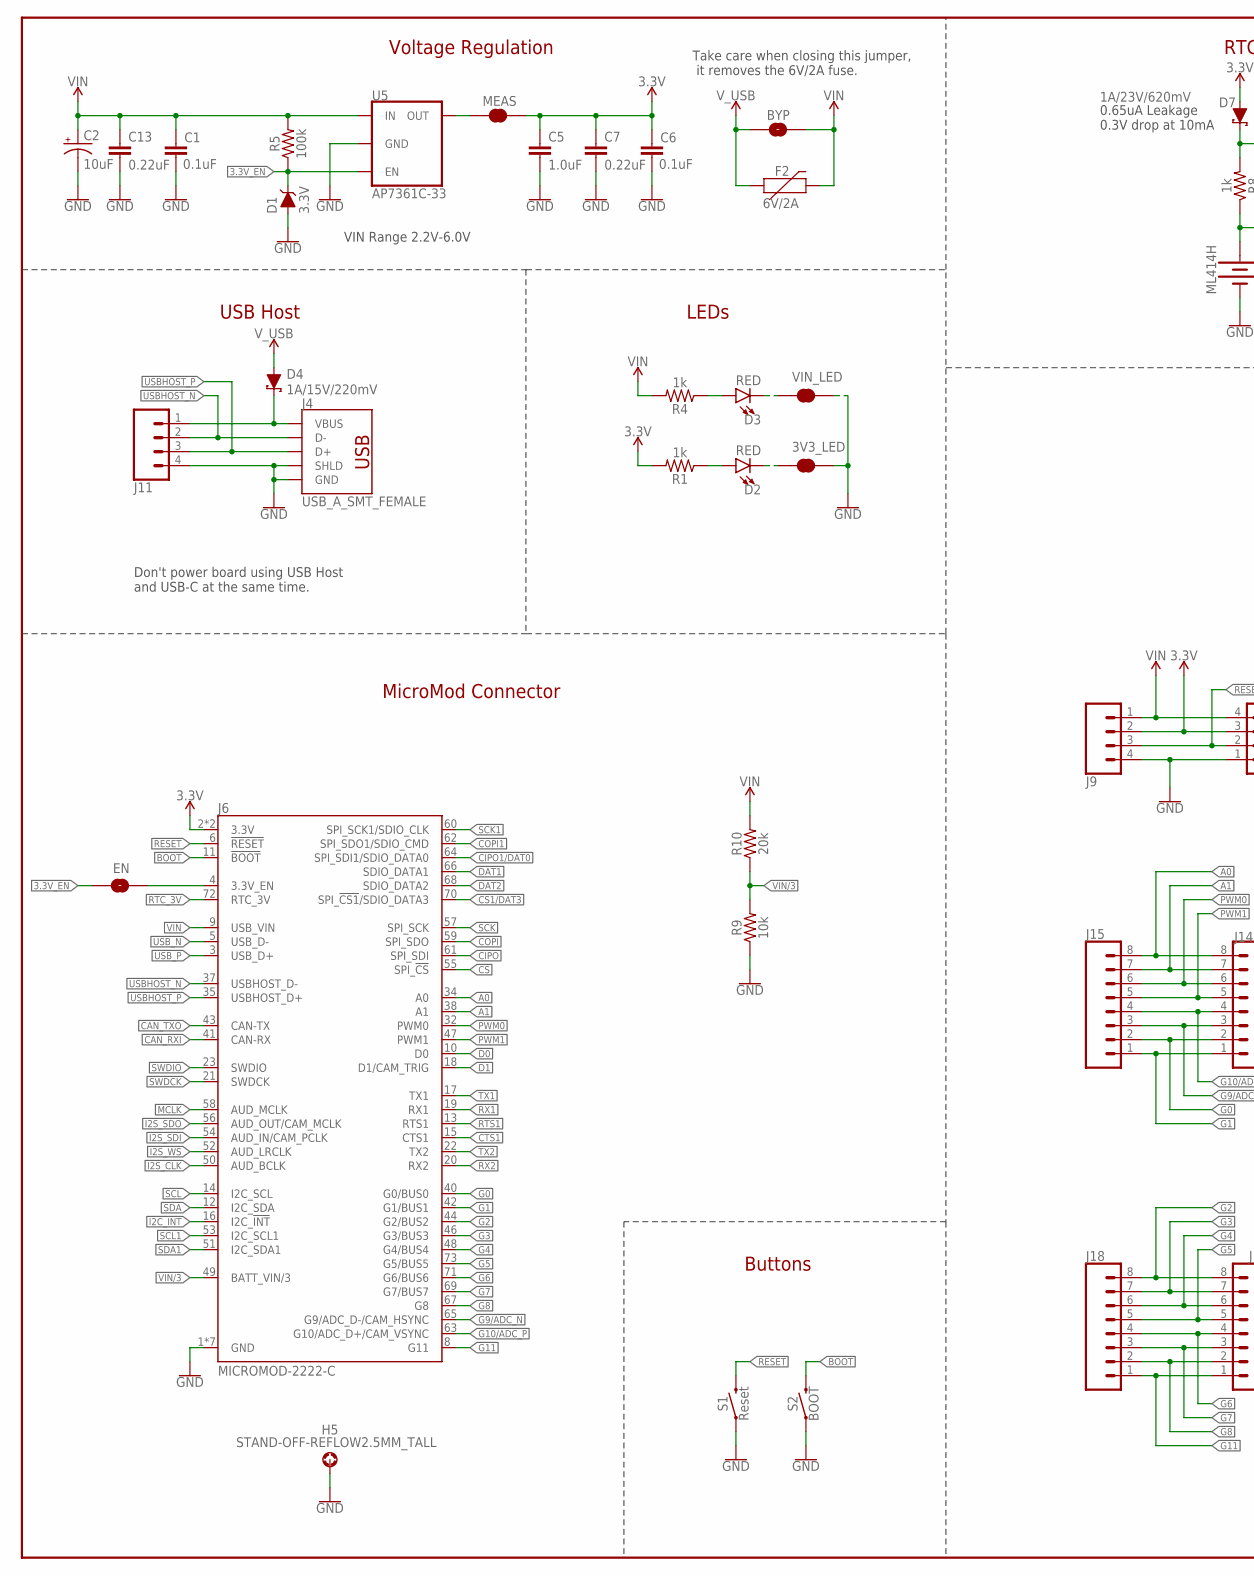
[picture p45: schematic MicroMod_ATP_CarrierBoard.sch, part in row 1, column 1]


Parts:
3V3_LED: JUMPER-SMT_2_NC_TRACE_SILK; SMT-JUMPER_2_NC_TRACE_SILK
BT1: ML414H; ML414H_IV01E
BYP: JUMPER-SMT_2_NO_SILK; SMT-JUMPER_2_NO_SILK
C1, C6: 0.1uF; 0603
C2: 10uF; EIA3216
C5: 1.0uF; 0603
C7, C13: 0.22uF; 0603
D1: 3.3V; SOD-323
D2, D3: RED; LED-0603
D4: 1A/15V/220mV; DO-214BA
D6: 3A/10V/280mV; SOD-323
D7: 1A/23V/620mV; SOD-323
EN: JUMPER-SMT_2_NO_SILK; SMT-JUMPER_2_NO_SILK
F2: 6V/2A; 1210
FD1, FD2, FD3, FD4: FIDUCIALUFIDUCIAL; FIDUCIAL-MICRO
FRAME1: FRAME-LEDGER; CREATIVE_COMMONS
H1, H2, H3, H4: STAND-OFF
H5: STAND-OFF-REFLOW2.5MM_TALL; STAND-OFF-REFLOW-M2.5
J1: USB_C_2-LAYER_PADS; USB-C-16P-2LAYER-PADS
J2: JTAG; 2X5-PTH-1.27MM
J3: CONN_05NO_SILK; 1X05_NO_SILK
J4: USB_A_SMT_FEMALE; USB-A-S-SILK-FEMALE
J6: MICROMOD-2222-C; M.2-CONNECTOR-E
J8, J21: 1X04_SMD_STRAIGHT_COMBO; 1X04_SMD_VERTICAL_COMBO
J9: CONN_041X04_NO_SILK; 1X04_NO_SILK
J10: CONN_05VERT_FEMALE_HEADER; 1X05_SMD_VERTICAL_COMBO
J11, J16, J22: CONN_041X04_NO_SILK_NO_POP; 1X04_NO_SILK
J12: CONN_12SMD_COMBINED; 1X12_SMD_COMBINED
J13: CONN_08NO_SILK_DNP; 1X08_NO_SILK
J14, J17, J24, J25: CONN_08SMD-COMBO-FEMALE; 1X08_SMD_COMBINED
J15, J18, J23, J26: CONN_08NO_SILK_FEMALE_PTH; 1X08_NO_SILK
J19, J20: QWIIC_RIGHT_ANGLE; JST04_1MM_RA
LOGO1: SFE_LOGO_NAME_FLAME.1_INCH; SFE_LOGO_NAME_FLAME_.1
LOGO2: QWIIC_LOGO_5MM; QWIIC_5MM
LOGO3: OSHW-LOGOMINI; OSHW-LOGO-MINI
MEAS: JUMPER-COMBO_2_NC_TRACE; COMBO-JUMPER_2_NC_TRACE
R1, R4, R8: 1k; 0603
R2, R3: 5.1k; 0603
R5: 100k; 0603
R9: 10k; 0603
R10: 20k; 0603
S1: Reset; TACTILE_SWITCH_SMD_5.2MM
S2: BOOT; TACTILE_SWITCH_SMD_5.2MM
TP1, TP2, TP3: TEST-POINT3X5; PAD.03X.05
U5: AP7361C-33; UDFN-8
VIN_LED: JUMPER-SMT_2_NC_TRACE_SILK; SMT-JUMPER_2_NC_TRACE_SILK

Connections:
3.3V: C5.1, C6.1, C7.1, D7.A, J2.1 (VCC), J3.4, J6.2 (3.3V), J6.74 (3.3V), J8.3, J9.2, J10.4, J12.1, J16.3, J19.2, J20.2, J21.3, J22.1, MEAS.2, MEAS.4 (2), R1.2
3.3V_EN: D1.C, EN.1, R5.1, U5.5 (EN)
!BOOT!: J6.11 (!BOOT!), S2.3 (2), S2.4 (2)
!CS1!/DAT3: J6.70 (SPI_!CS1!/SDIO_DATA3), J12.7, J13.6
!CS!: J6.55 (SPI_!CS!), J12.3, J22.3
!RESET: J2.10 (!RESET), J6.6 (!RESET!), J8.2, J9.3, S1.3 (2), S1.4 (2)
A0: J6.34 (A0), J14.8, J15.8
A1: J6.38 (A1), J14.7, J15.7
CAN_RXI: J6.41 (CAN-RX), J25.2, J26.2
CAN_TXO: J6.43 (CAN-TX), J25.3, J26.3
CIPO: J6.61 (SPI_SDI), J12.6, J13.7
CIPO1/DAT0: J6.64 (SPI_SDI1/SDIO_DATA0), J12.10, J13.3
COPI: J6.59 (SPI_SDO), J12.5, J13.8
COPI1: J6.62 (SPI_SDO1/SDIO_CMD), J12.11, J13.2
CTS1: J6.15 (CTS1), J23.7, J24.7
D0: J6.10 (D0), J25.6, J26.6
D1: J6.18 (D1/CAM_TRIG), J25.7, J26.7
DAT1: J6.66 (SDIO_DATA1), J12.9, J13.4
DAT2: J6.68 (SDIO_DATA2), J12.8, J13.5
G0: J6.40 (G0/BUS0), J14.2, J15.2
G1: J6.42 (G1/BUS1), J14.1, J15.1
G2: J6.44 (G2/BUS2), J17.8, J18.8
G3: J6.46 (G3/BUS3), J17.7, J18.7
G4: J6.48 (G4/BUS4), J17.6, J18.6
G5: J6.73 (G5/BUS5), J17.5, J18.5
G6: J6.71 (G6/BUS6), J17.4, J18.4
G7: J6.69 (G7/BUS7), J17.3, J18.3
G8: J6.67 (G8), J17.2, J18.2
G9/ADC_N: J6.65 (G9/ADC_D-/CAM_HSYNC), J14.3, J15.3
G10/ADC_P: J6.63 (G10/ADC_D+/CAM_VSYNC), J14.4, J15.4
G11: J6.8 (G11), J17.1, J18.1
GND: 3V3_LED.2, BT1.-, C1.2, C2.-, C5.2, C6.2, C7.2, C13.2, D1.A, H5.1, J1.GND, J1.GND2 (GND), J2.3 (GND), J2.5 (GND), J2.9 (GND), J3.5, J4.GND, J4.SHLD1 (SHLD), J4.SHLD2 (SHLD), J6.1 (GND), J6.7 (GND), J6.33 (GND), J6.36 (GND), J6.39 (GND), J6.45 (GND), J6.75 (GND), J8.1, J9.4, J10.5, J11.4, J12.2, J16.4, J19.1, J20.1, J21.4, J22.2, J25.8, J26.8, R2.1, R3.1, R9.1, S1.1, S1.2 (1), S2.1, S2.2 (1), U5.4 (GND), U5.EP (GND), VIN_LED.2
I2C_!INT: J3.1, J6.16 (I2C_!INT!), J10.1
I2S_CLK: J6.50 (AUD_BCLK), J23.5, J24.5
I2S_SDI: J6.54 (AUD_IN/CAM_PCLK), J23.3, J24.3
I2S_SDO: J6.56 (AUD_OUT/CAM_MCLK), J23.2, J24.2
I2S_WS: J6.52 (AUD_LRCLK), J23.4, J24.4
MCLK: J6.58 (AUD_MCLK), J23.1, J24.1
unnamed: D2.A, R1.1
unnamed: D3.A, R4.1
unnamed: 3V3_LED.1, D2.C
unnamed: D3.C, VIN_LED.1
unnamed: EN.2, J6.4 (3.3V_EN)
unnamed: D4.C, J4.VBUS, J11.1
unnamed: J1.A5 (CC1), R2.2
unnamed: J1.B5 (CC2), R3.2
unnamed: BT1.+, D6.A, R8.1
OUT_MEAS: MEAS.1, MEAS.3 (1), U5.1 (OUT)
PWM0: J6.32 (PWM0), J14.6, J15.6
PWM1: J6.47 (PWM1), J14.5, J15.5
RTC_3V: D6.C, D7.C, J6.72 (RTC_3V), R8.2, TP1.P$1
RTS1: J6.13 (RTS1), J23.6, J24.6
RX1: J6.19 (RX1), J25.1, J26.1
RX2: J6.20 (RX2), J25.5, J26.5
SCK: J6.57 (SPI_SCK), J12.4, J22.4
SCK1: J6.60 (SPI_SCK1/SDIO_CLK), J12.12, J13.1
SCL: J3.2, J6.14 (I2C_SCL), J10.2, J20.4
SCL1: J6.53 (I2C_SCL1), J16.1, J19.4, J21.1
SDA: J3.3, J6.12 (I2C_SDA), J10.3, J20.3
SDA1: J6.51 (I2C_SDA1), J16.2, J19.3, J21.2
SWDCK: J2.4 (SWDCLK), J6.21 (SWDCK), TP3.P$1
SWDIO: J2.2 (SWDIO), J6.23 (SWDIO), TP2.P$1
TX1: J6.17 (TX1), J23.8, J24.8
TX2: J6.22 (TX2), J25.4, J26.4
USBHOST_N: J4.D-, J6.37 (USBHOST_D-), J11.2
USBHOST_P: J4.D+, J6.35 (USBHOST_D+), J11.3
USB_N: J1.A7 (D-), J1.B7 (D-), J6.5 (USB_D-)
USB_P: J1.A6 (D+), J1.B6 (D+), J6.3 (USB_D+)
VIN: BYP.2, C1.1, C2.+, C13.1, F2.2, J6.9 (USB_VIN), J8.4, J9.1, R4.2, R5.2, R10.2, U5.8 (IN)
VIN/3: J6.49 (BATT_VIN/3), R9.2, R10.1
V_USB: BYP.1, D4.A, F2.1, J1.VBUS1 (VBUS), J1.VBUS2 (VBUS)

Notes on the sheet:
300uA Leakage
0.65uA Leakage 0.3V drop at 10mA
~20 minute charge time
1mAhr Capacity
Take care when closing this jumper, it removes the 6V/2A fuse.
SWD
USB
Headers
RTC
Voltage Regulation
MicroMod Connector
Elias Santistevan
LEDs
USB Host
Buttons
v11
VIN Range 2.2V-6.0V
Don't power board using USB Host and USB-C at the same time.
Testpoints



Board: 2 copper layers, 86.4 x 55.9 mm, 222 parts (80 on the bottom side), 71 nets.

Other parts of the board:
H6, H7: STAND-OFF
LOGO4: SFE_LOGO_NAME_FLAME.2_INCH; SFE_LOGO_NAME_FLAME_.2
LOGO5, LOGO6, LOGO7, LOGO8: QWIIC_LOGO_3MM; QWIIC_5MM
U$1, U$123: #A0#10
U$2, U$124: #A1#10
U$3, U$27, U$46, U$47, U$58, U$89, U$100, U$101, U$102, U$103, U$104, U$105: #GND#0
U$4, U$120: #G0#2
U$5: #RESET10
U$6, U$98: #D0#0
U$7, U$119: #G1#2
U$8, U$118: #G2#2
U$9, U$117: #G3#3
U$10, U$116: #G4#4
U$11, U$115: #G5#5
U$12, U$114: #G6#6
U$13, U$113: #G7#7
U$14, U$112: #G8#8
U$15: #G9#9
U$16: #G10#10
U$17, U$111: #G11#10
U$18, U$121: #PWM0#10
U$19, U$122: #PWM1#10
U$20: ##CS1##5178039
U$21, U$110: ##I2C_INT##10
U$22: #CAN_RX#9
U$23, U$97: #CAN_TX#10
U$24: #CIPO#3
U$25: #COPI#2
U$26: #CTS#6
U$28: #SCK#2
U$29: #I2S_FS#5
U$30: #I2S_SDI#5
U$31: #I2S_SDO#5
U$32: #MCLK#4
U$33: #RTS#5
U$34: #RX#8
U$35: #TX#7
U$36: #DAT1#5178039
U$37, U$125: ##RESET##7
U$38, U$60, U$61, U$70, U$88, U$106, U$107, U$126: #3V3#1
U$39: #BYP#8
U$40, U$128: #HOST_D##9
U$41, U$129: #HOST_D##10
U$42, U$132: #MEAS#10
U$43: BOOT10
U$44, U$108: #SDA#4
U$45, U$127: #VIN#6
U$48: #EN#0
U$49, U$109: #SCL#5
U$50, U$146: #VHOST#0
U$51, U$131: #SWD#10
U$52: #I2S_CLK#5
U$53: #DAT2#5178039
U$54: #CIPO1#5178039
U$55: 22229
U$56: ##CIPO1##DAT0#5178038
U$57, U$75: #COPI1#2
U$59: ##CS##0
U$62: ATP0
U$63, U$76: #RX2#3
U$64, U$80: #TX2#2
U$65, U$78: #SCL1#3
U$66, U$79: #SDA1#3
U$67, U$77: #SCK1#2
U$68: VIN3
U$69: 3V34
U$71: I2C4
U$72: I2C14
U$73: ATP_CARRIER_BOARD1
U$81: ##CS##5178037
U$82: #DAT2#5
U$83: #DAT1#5
U$84: ##CS1##DAT3#5178037
U$85: #COPI#4
U$86: #SCK#4
U$87: #MCLK#6
U$90: #I2S_FS#7
U$91: #I2S_CLK#7
U$92: #RTS#7
U$93: #CTS#8
U$94: #TX#9
U$95: #RX#10
U$96: #CAN_RX#10
U$99, U$145: D10
U$133: #VIN_LED#10
U$134: #3V3_LED#10
U$135: #G9#ADC##CAM_HSYNC#9
U$136: #G10#ADC##CAM_VSYNC#10
U$137: #I2S_SDI#CAM_PCLK#7
U$138: #I2S_SDO#CAM_MCLK#7
U$139, U$141, U$142, U$143: MOUNT10
U$140: MICROMOD_MI_LOGO_1
U$144: MICROMOD_LOGO_1
U$147: #CIPO#5178038

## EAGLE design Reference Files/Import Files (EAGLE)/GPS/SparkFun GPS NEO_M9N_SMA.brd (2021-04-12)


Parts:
B1: 6.8MM_COIN_CELL; ML414H_IV01E
C1: 47pF; 0402
C3, C4, C6: 1.0uF; 0603
C5: 0.1uF; 0603
D2: 0.5A/40V/420mV; SOD-323
D3: PRTR5V0U2F; SOT886
E1: ANTENNA-GROUNDEDEDGE_SMA_SMD; SMA-EDGE-SMD
FB1: FERRITE_BEAD-120_OHM-0402; 0402
FRAME1: FRAME-LETTER; CREATIVE_COMMONS
J1: CONN_07NO_SILK; 1X07_NO_SILK
J2, J4: Qwiic Right Angle; JST04_1MM_RA
J3: USB_C_2-LAYER_PADS; USB-C-16P-2LAYER-PADS
J5: CONN_041X04_NO_SILK_NO_POP; 1X04_NO_SILK
JP1, JP31, JP91, JP101: STAND-OFF
JP5: JUMPER-SMT_3_2-NC_TRACE_SILK; SMT-JUMPER_3_2-NC_TRACE_SILK
JP15: CONN_041X04_NO_SILK_NO_POP; 1X04_NO_SILK
JP21, JP61, JP71, JP81: FIDUCIALUFIDUCIAL; MICRO-FIDUCIAL
LED1: BLUE; LED-0603
LED2: RED; LED-0603
LOGO1: OSHW-LOGOMINI; OSHW-LOGO-MINI
LOGO2: SFE_LOGO_NAME_FLAME.1_INCH; SFE_LOGO_NAME_FLAME_.1
PPS: JUMPER-SMT_2_NC_TRACE_SILK; SMT-JUMPER_2_NC_TRACE_SILK
PWR\: JUMPER-SMT_2_NC_TRACE_SILK; SMT-JUMPER_2_NC_TRACE_SILK
R1, R5, R11: 1k; 0603
R2, R3, R4, R6: 33; 0603
R7, R8: 2.2k; 0603
R9, R10: 27; 0603
R12, R13: 5.1k; 0603
R14: 33; 0402
R15: 100k; 0603
R16: 10k; 0402
SPI: JUMPER-SMT_2_NO_SILK; SMT-JUMPER_2_NO_SILK
TP1: TEST-POINT3X4; PAD.03X.04
U1: U-BLOX_NEO-M9N; NEO-M9N/M8T/M8U
U2: 3.3V; SOT23-5

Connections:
3.3V: C4.1, C5.2, D2.A, J1.3, J2.2, J4.2, J5.2, JP5.2, PWR\.2, R15.2, R16.2, U1.7 (VDD_USB), U1.23 (VCC), U2.5 (OUT)
5V: C6.1, D3.5, J1.2, J3.VBUS1 (VBUS), J3.VBUS2 (VBUS), U2.1 (IN), U2.3 (EN)
!RESET: JP15.3, U1.8 (!RST)
!SAFE: JP15.2, U1.1 (!SAFEBOOT!)
D+: D3.4, R9.1
D-: D3.6, R10.1
D_SEL: R16.1, SPI.2, U1.2 (D_SEL)
GND: B1.-, C1.2, C3.2, C4.2, C5.1, C6.2, D3.2, E1.GND@0 (GND), E1.GND@1 (GND), J1.1, J2.1, J3.GND, J3.GND2 (GND), J4.1, J5.1, LED1.C, LED2.C, R12.1, R13.1, R15.1, SPI.1, U1.10 (GND), U1.12 (GND), U1.13 (GND), U1.24 (GND), U2.2 (GND)
GPS_ANT1: E1.SIG (SIGNAL), FB1.1, U1.11 (RF_IN)
INT: JP15.1, U1.4 (EXT_INT)
unnamed: PWR\.1, R1.2
unnamed: LED1.A, R11.1
unnamed: C1.1, FB1.2, R14.1
unnamed: PPS.1, R11.2
unnamed: JP5.1, R8.2
unnamed: D2.C, R5.2
unnamed: J3.B5 (CC2), R12.2
unnamed: JP5.3, R7.2
unnamed: J3.A5 (CC1), R13.2
unnamed: LED2.A, R1.1
unnamed: R9.2, U1.6 (USB_D+)
unnamed: R10.2, U1.5 (USB_D-)
PPS: JP15.4, PPS.2, U1.3 (TIMEPULSE)
RXI/SDI: J1.5, R6.2
RXLV: R6.1, U1.21 (RX/SPI_MOSI)
SCL/SCK: J1.7, J2.4, J4.4, J5.4, R4.2, R7.1
SCL_LV: R4.1, U1.19 (SCL/SPI_CLK)
SDA/!CS: J1.4, J2.3, J4.3, J5.3, R2.2, R8.1
SDA_LV: R2.1, U1.18 (SDA/SPI_!CS!)
SHLD: J3.SHLD1 (SHLD), J3.SHLD2 (SHLD), J3.SHLD3 (SHLD), J3.SHLD4 (SHLD)
TXLV: R3.1, U1.20 (TX/SPI_MISO)
TXO/SDO: J1.6, R3.2
USB_D+: D3.3, J3.A6 (D+), J3.B6 (D+)
USB_D-: D3.1, J3.A7 (D-), J3.B7 (D-)
VCC_RF: R14.2, U1.9 (VCC_RF)
V_BATT: B1.+, C3.1, R5.1, TP1.P$1, U1.22 (V_BKCP)

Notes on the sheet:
V10
7-bit unshifted I2C address: 0x42
Cut jumper to remove I2C pullups from bus
Cut jumpers to disable LEDs
Close SPI jumper to enable SPI
Elias Santistevan
Headers
LEDs and Jumpers
Hot Start Battery
GPS: u-Blox NEO-M9N
SMA Connector
USB Connector - Power
VCC Range: 2.7V - 3.3V
VCC Range: 2.5V - 6V 600mA Output
For best results use an antenna that supports both L1/L2 bands.



Board: 2 copper layers, 40.6 x 36.8 mm, 94 parts (31 on the bottom side), 36 nets.

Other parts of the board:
U$1: ##CS##9
U$2: U#BLOX19
U$3: ##SAFE##15
U$4, U$5, U$39, U$40: #3V3#6
U$6, U$42: #5V#1
U$7, U$8, U$38, U$41: #GND#0
U$9: #INT#16
U$10: PPS7
U$11, U$32: #PPS#13
U$12: #SPI#22
U$13: PWR6
U$14: QWIIC_4MM
U$15: #RX#SDI#10
U$16: #SCK#12
U$17: #PWR#1
U$18: #SCL#18
U$19: #SDA#17
U$20: #TX#SDO#11
U$21: NEO_GPS_BOARD_SILK_FINAL#03#JPG
U$22: ##SAFE##11
U$23: L1#L28
U$24: ANT8
U$25: NEO#M9N20
U$26: ##CS##6
U$27: ##RST##12
U$28: ##RST##2
U$29: #I2C#3
U$30: #INT#10
U$31: #PPS#0
U$33: #RX#SDI#4
U$34: #SCK#3
U$35: #SCL#8
U$36: #SDA#9
U$37: #TX#SDO#5

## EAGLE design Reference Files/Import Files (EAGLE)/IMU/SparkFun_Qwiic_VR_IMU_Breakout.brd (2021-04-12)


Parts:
C1, C2, C4: 0.1uF; 0603
C3, C5: 22pF; 0603
D1: RED; LED-0603
FRAME1: FRAME-LETTER; CREATIVE_COMMONS
J1: CONN_06NO_SILK_FEMALE_PTH; 1X06_NO_SILK
J2, J4: SMD; 1X04_1MM_RA
J3: PTH; 1X04_NO_SILK
J5: CONN_01PTH_NO_SILK_YES_STOP; 1X01_NO_SILK
J6: SPI; 1X08_NO_SILK
J7, J8: CONN_021X02_NO_SILK; 1X02_NO_SILK
JP1, JP2, JP5, JP6: FIDUCIALUFIDUCIAL; MICRO-FIDUCIAL
JP3, JP4: STAND-OFF
LOGO1: OSHW-LOGOMINI; OSHW-LOGO-MINI
LOGO2: REVISION
LOGO4: SFE_LOGO_FLAME.1_INCH; SFE_LOGO_FLAME_.1
LOGO5: SFE_LOGO_NAME_FLAME.1_INCH; SFE_LOGO_NAME_FLAME_.1
R1, R3, R6, R7, R8: 10k; 0603
R2: 1k; 0603
R9, R10: 4.7k; 0603
R12, R13: 2.2k; 0603
SJ1: JUMPER-SMT_3_2-NC_PASTE_SILK; SMT-JUMPER_3_2-NC_PASTE_SILK
SJ2, SJ3, SJ4: SOLDERJUMPERNO; SJ_2S-NO
U2: BNO080; LGA-28
Y1: 32.768kHz; CRYSTAL-SMD-3.2X1.5MM

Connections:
3.3V: C2.1, C4.1, D1.A, J1.3, J2.2 (VCC), J3.2 (VCC), J4.2 (VCC), J6.2, R1.2, R3.2, R6.2, R9.2, R10.2, SJ1.2, SJ3.1, SJ4.1, U2.3 (VDD), U2.28 (VDDIO)
!BOOT: J5.1, R6.1, U2.4 (!BOOT)
!CS: J6.6, U2.18 (!H_CS)
!INT: J7.2, U2.14 (!H_INT)
!RST: J6.8, J7.1, R1.1, U2.11 (!RST)
ADDR/MOSI: J6.5, R3.1, SJ2.2, U2.17 (H_SA0/MOSI)
CAP: C1.1, U2.9 (CAP)
GND: C1.2, C2.2, C3.2, C4.2, C5.2, J1.1, J2.1 (GND), J3.1 (GND), J4.1 (GND), J6.1, R2.1, R7.1, R8.1, SJ2.1, U2.2 (GND), U2.10 (CLKSEL0), U2.25 (GNDIO)
unnamed: C5.1, U2.27 (XIN32), Y1.P$2 (2)
unnamed: C3.1, U2.26 (CLKSEL1), Y1.P$1 (1)
unnamed: D1.C, R2.2
PS0/WAKE: J6.7, J8.2, R7.2, SJ3.2, U2.6 (PS0/WAKE)
PS1: J8.1, R8.2, SJ4.2, U2.5 (PS1)
SCL/SCK/RX: J1.4, J2.4 (SCL), J3.4 (SCL), J4.4 (SCL), J6.3, R12.1, U2.19 (H_SCL/SCLK/RX)
SCL_PU: R12.2, SJ1.1
SDA/MISO/TX: J1.5, J2.3 (SDA), J3.3 (SDA), J4.3 (SDA), J6.4, R13.1, U2.20 (H_SDA/MISO/TX)
SDA_PU: R13.2, SJ1.3
S_SCL: R10.1, U2.15 (S_SCL)
S_SDA: R9.1, U2.16 (S_SDA)

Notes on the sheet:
N. Seidle
v10
7-Bit I2C Address Jumper
Closed = 0x4A
Open (default) = 0x4B
PS0 0 1 0 1
PS1 0 0 1 1
Interface I2C UART-RVC UART SPI
The default is I2C
Clear SJ1 when using SPI or UART
I C
UART
SPI
Power
A. England
Supply Voltage: 2.4V-3.6V



Board: 2 copper layers, 30.5 x 25.4 mm, 89 parts (35 on the bottom side), 19 nets.

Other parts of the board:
U$1: (PWR)
U$2: BOOT2
U$3, U$4: #RST>
U$5, U$6: SCL
U$7, U$8: SDA
U$9, U$10: 3V3
U$11, U$50: 3V30
U$12, U$13: SCK0
U$14: PS03
U$15, U$16: GND
U$17, U$18: SI1
U$19, U$20: #WAK6
U$21: 3V32
U$22: RXI1
U$23: (I_SUPER2_C)
U$25, U$26: #INT0
U$27, U$28: PS14
U$29: PS05
U$30: ADR0
U$33: PS114
U$34: PS015
U$35: TXO0
U$39: UART8
U$40: GRN10
U$41: BLK9
U$42, U$43: GND1
U$44: BNO080_IMU11
U$46: BNO08012
U$47: IMU13
U$49, U$51: #RST7
U$52, U$53: #CS3
U$54, U$55: SO0
U$59: QWIIC#LABEL#FULL#M#PNG

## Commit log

2021-04-12 Altium file and picture uploads
    Uploaded screen shots of measured dimensions from Altium Designer Project
    [MicroMod_ATP_CarrierBoard.PcbDoc, MicroMod_ATP_CarrierBoard.PrjPcb, MicroMod_ATP_CarrierBoard.brd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]
2021-04-12 Useful files for PCB design
    These files can be used to gather measurements to ensure proper placement of components.
    [MicroMod_ATP_CarrierBoard.brd, MicroMod_ATP_CarrierBoard.sch, Qwiic Pressure Sensor - LPS25HB.PcbDoc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]
2021-04-29 File organization
    [MicroMod_ATP_CarrierBoard.PcbDoc, MicroMod_ATP_CarrierBoard.PrjPcb, MicroMod_ATP_CarrierBoard.brd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]
2021-05-04 SparkFun Library upload
    This includes the addition of SparkFun's Eagle libraries which we will use in Altium. You will need to use the import wizard to first convert the .lbr files to .pcblib and .schlib files.
    [SparkFun_Qwiic_VR_IMU_Breakout.SchDoc.SchDoc]
2021-05-05 Work Done 5/4
    Replaced a few reference files. Created libraries for sensors ("User Made"). Downloaded and made libraries from SparkFun accessible. Version 1 of PCB_Shield project has been created. Initial layout for carrier pins has been created in the PCB_Shield schematic and have been roughly placed in the PCB document.
    [MicroMod_ATP_CarrierBoard.PrjPcb, MicroMod_ATP_CarrierBoard.SchDoc, PCB_Shield.PrjPcb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]
2021-05-05 Saved Document
    [PCB_Shield.PrjPcb]
2021-05-05 Finished PCB Shield Version 1
    Version 1 of the PCB shield includes only the header pins that will be connected to the board.
    [PCB_Shield_v1.PcbDoc]
2021-05-05 Resolved Design Rule Errors
    No duplicate TX2 pin. TX replaced the duplicate. Max hole size rule changed to allow mounting holes.
    [PCB_Shield_v1.PcbDoc, Shield_Schematic.SchDoc]
2021-05-07 Work 5/7
    More libraries were added (adafruit and user made). First version/layout of PCB is almost done. Power regulation on board still needs to be drawn in schematic and laid out on the PCB.
    [MachineLearning-MM-Carrier.PcbDoc, MachineLearning-MM-Carrier.PrjPcb, MachineLearning-MM-Carrier.SchDoc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]
2021-05-07 Work 5/7
    Small change adding the word "Male" on top overlay to in order to clarify using a male XT30 connector for powering avionics board.
    [PCB_Shield_v1.PcbDoc]
2021-05-07 Added Logos
    Folder containing logos has been added. The UF DBF logo has also been added to the top overlay on the PCB.
    [PCB_Shield.PrjPcb, PCB_Shield_v1.PcbDoc, Shield_Schematic.SchDoc]
2021-05-07 Fixed Alarm and Bal 6s connections
    Also added the rest of sparkFun's libraries.
    [MicroMod_ATP_CarrierBoard.PrjPcb, MicroMod_ATP_CarrierBoard.SchDoc, PCB_Shield_v1.PcbDoc]
2021-05-08 v1 complete and added libraries
    v1 of board is complete with no design rule errors. Next version will better address design rules for fabrication and minimum spec. Layout can be much improved. Libraries added were for LM338.
    [PCB_Shield_v1.PcbDoc, Shield_Schematic.SchDoc]
2021-05-08 v1 5/8
    Most recent version of board
    [Componet List.xlsx, PCB_Shield_v1.PcbDoc]
2021-05-09 Addition of 3D models and .STEP and .STP files
    [1053091202.stp, LM338_NOPB.STEP, PCB_Shield_v1.PcbDoc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]
2021-05-09 CAD files for triple row male header pins
    [3x1 Male Pin Header Angle.STEP, 3x1 Male Pin Header.STEP, 3x10 Male Pin Header Angle.STEP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]
2021-05-15 Update to v1 & DBF library creation
    Updates to schematics includes brief notes about what to add for v2. DBF library will include all parts and schematics required to complete board.
    [10-Pin Header - Female - 2.54mm.step, 11-Pin Header - Female - 2.54mm.step, 12-Pin Header - Female - 2.54mm.step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]
2021-05-15 LMZ12002 Reference Files
    Includes schematic, Design Reports, Parts List, Export Files for Altium. This was all created using TI WEBENCH® Designer using the following specs. Vin(7-8.6V) Vout(5V) Iout(1A) Ambient Temp (35 deg.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
    [WBBOMDesign4_Parts_List.csv, WBOperatingValuesDesign4.csv]
2021-05-23 Update 5/23
    More components added to DBF library, source files for footprints and 3D models, and file organization under library folder.
    [C3216X5R1A107M160AC.STEP, ERJ-6ENF1071V.STEP, GRM1555C1H102JA01J.STEP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]
2021-05-31 5/31 Update
    LEDs for status indication and testing/debugging have been selected and added to the DBF libraries. Work on v2 schematic will be starting.
    [150080AS75000_Download_STP_WL-SMCW-0805_rev1.stp, Componet List.xlsx]
2021-05-31 Update Componet List.xlsx
    Added part number for current limiting resistor for LEDs
    [Componet List.xlsx]
2021-06-01 Update 6/1
    1st draft for schematic v2 is complete, and PCB design for v2 is about 50% complete. Footprints in DBF library have been improved/revised.
    [PCB-Shield_v2.PcbDoc, PCB_Shield.PrjPcb, PCB_Shield_v1.PcbDoc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]
2021-06-01 Update 6/1
    Finished 1st draft of v2
    [PCB-Shield_v2.PcbDoc, PCB_Shield.PrjPcb, PCB_Shield_v1.PcbDoc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]
2021-06-01 Update 6/1
    Removed dead copper and increased buck converter's conductor width (pin 8 connection to ground) from 10mil to 100mil
    [PCB-Shield_v2.PcbDoc]
2021-06-01 Update 6/1
    Fixed more conductor widths.
    [PCB-Shield_v2.PcbDoc, Shield_Schematic_v2.SchDoc]
2021-06-25 Update 6/25
    Thermal Relief Connections have been adjusted in the DBF library for the appropriate components.
    [PCB-Shield_v2.PcbDoc]
2021-08-10 Update Componet List.xlsx
    [Componet List.xlsx]
2021-08-26 Created "Figures" folder
    Includes logos and images of current PCB for v2
2022-03-30 Consolidated user made libraries and added components for V3.
    [693071030811_microSD.stp, Componet List.xlsx, PCB_Shield_v3.PrjPcb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]

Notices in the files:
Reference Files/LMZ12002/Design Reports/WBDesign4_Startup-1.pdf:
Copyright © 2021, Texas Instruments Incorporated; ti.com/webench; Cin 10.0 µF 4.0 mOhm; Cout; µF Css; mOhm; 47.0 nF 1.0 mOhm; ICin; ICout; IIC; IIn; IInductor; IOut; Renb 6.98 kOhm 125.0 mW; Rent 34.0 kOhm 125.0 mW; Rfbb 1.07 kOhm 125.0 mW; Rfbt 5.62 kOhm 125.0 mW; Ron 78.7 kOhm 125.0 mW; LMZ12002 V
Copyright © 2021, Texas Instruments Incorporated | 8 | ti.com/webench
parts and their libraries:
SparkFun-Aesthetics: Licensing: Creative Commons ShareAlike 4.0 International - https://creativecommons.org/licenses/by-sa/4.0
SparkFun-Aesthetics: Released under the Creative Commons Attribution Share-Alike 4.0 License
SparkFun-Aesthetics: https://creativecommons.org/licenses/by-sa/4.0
